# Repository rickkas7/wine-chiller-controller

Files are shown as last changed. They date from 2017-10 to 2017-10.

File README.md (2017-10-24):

# Wine chiller controller replacement

I have two Edgestar TWR282S thermoelectric wine chillers. One has wine in it, but the other I keep vegetables in, sort of like a root cellar.

They're over 10 years old, and I've been replacing parts on them for a while, but the case and doors are fine and the vegetable one has custom plexiglass shelves in it, so I hesitate to replace it.

I've replaced interior fans, [exterior fans](http://blog.rickk.com/food/2014/12/wine-chiller-exterior-fan-repair.html), and [Peltier chillers](http://blog.rickk.com/food/2013/06/repairing-a-wine-chiller.html), which are all pretty straightforward to do.

I also replaced the [controller boards](http://blog.rickk.com/food/2013/10/repairing-a-wine-chiller-part-2.html), which were available from Edgestar. They were kind of expensive at $48, and apparently not very durable, because one of the 4 year old replacements failed. And they're no longer available.

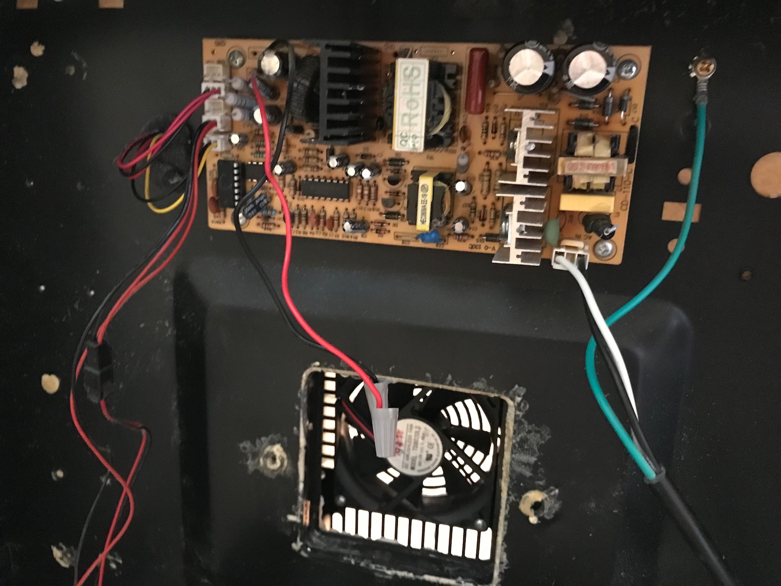
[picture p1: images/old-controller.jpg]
old controller


It appears the inductor failed. I might be able to just replace that but I have a better idea.

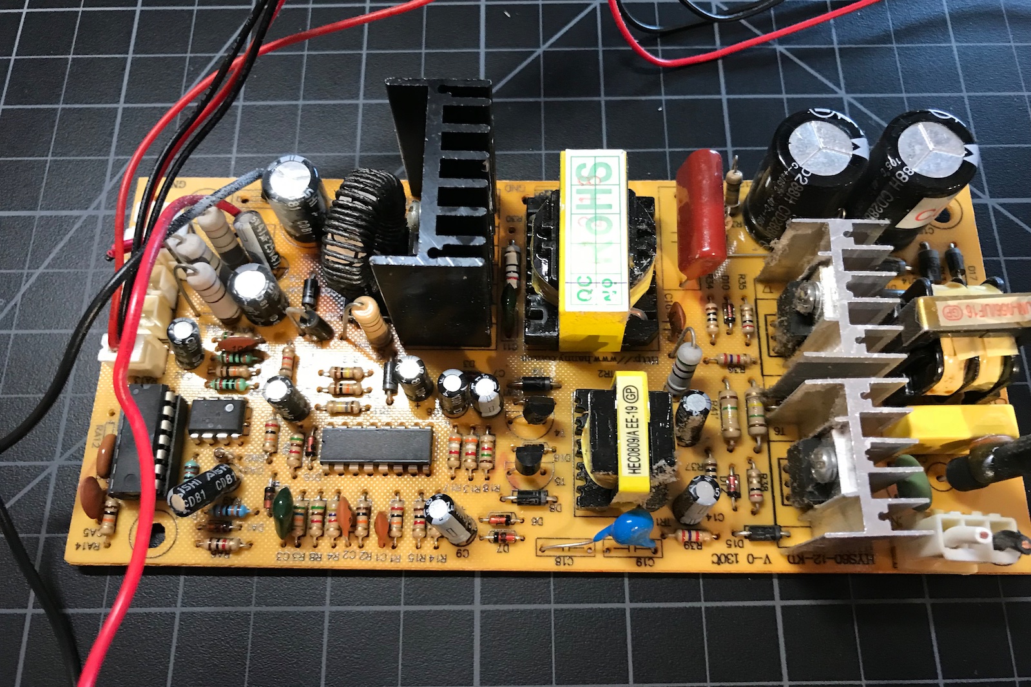
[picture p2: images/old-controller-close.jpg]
old controller close-up


I added a new power supply, controller board, and a fancy display that shows the temperature and also communicates the data so I can monitor the temperatures remotely!

The cyan LED to the right of the alphanumeric display turns red when the temperature is out of normal range.

I also get push notifications on my phone if the temperature goes way out of normal range.

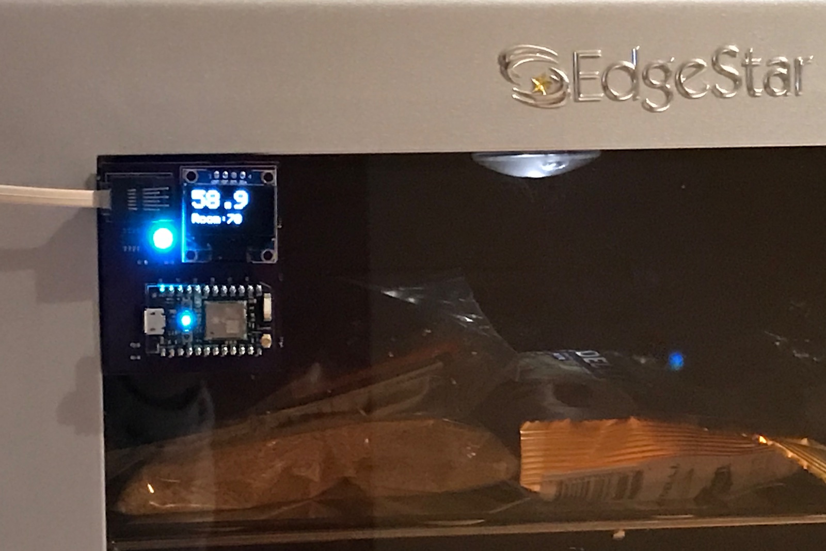
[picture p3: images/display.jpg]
display


## Power Supply

I replaced the power supply with a $14.98 12V 10A switching power supply that I got [from Amazon](https://www.amazon.com/LEDMO-Switching-Converter-Adapter-Transformer/dp/B01E6RMASC/ref=pd_ybh_a_4). It really only needs to be 5 to 6A, but the 10A was reasonably priced and offers a nice safety margin.

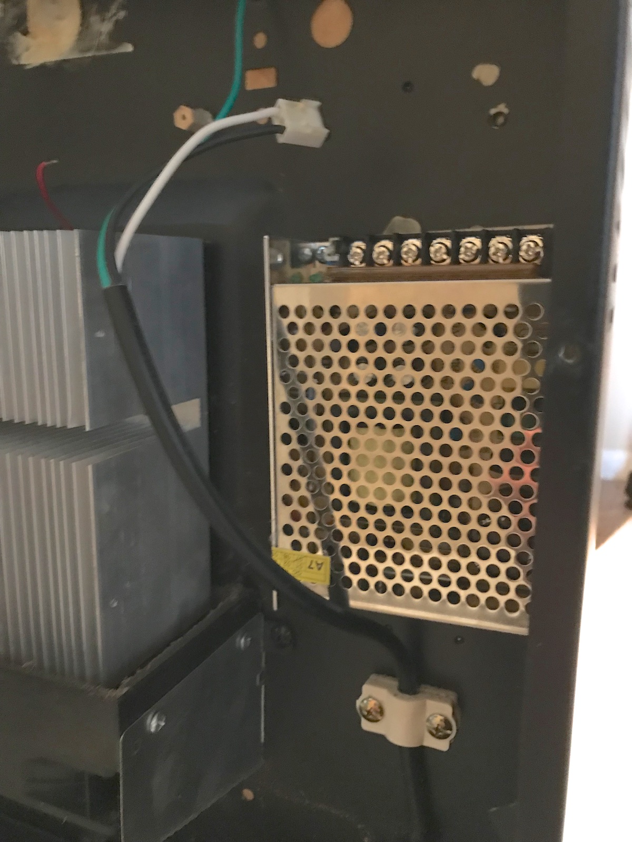
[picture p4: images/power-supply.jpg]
power supply


I was able to use the existing power cord, and I just replaced the connector with two spade lugs for connecting to the power supply. I also moved it from above the Peltier heat sink to the side, so hot air is not constantly blowing across it. The old location really seems suboptimal.

## Power Board

I made a power/controller board as well. It has a power supply for the display board, a bunch of handy connectors, a fuse, and a relay. 

In practice the Peltier is always on in my experience, but I did add a relay so it could be turned off in software, based on the thermometer reading inside the chiller. This allows for temperature control, and would also save some energy, as the Peltier by far uses the most energy, about 48 watts.
 
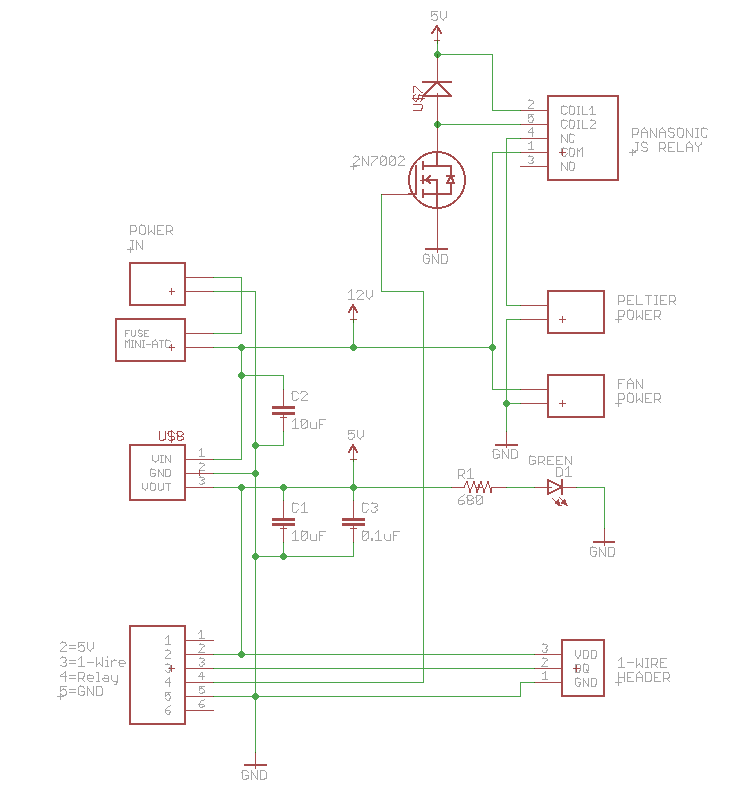
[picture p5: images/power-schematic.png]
power board schematic

 
This is the controller board with the 7 SMD components soldered to the board.

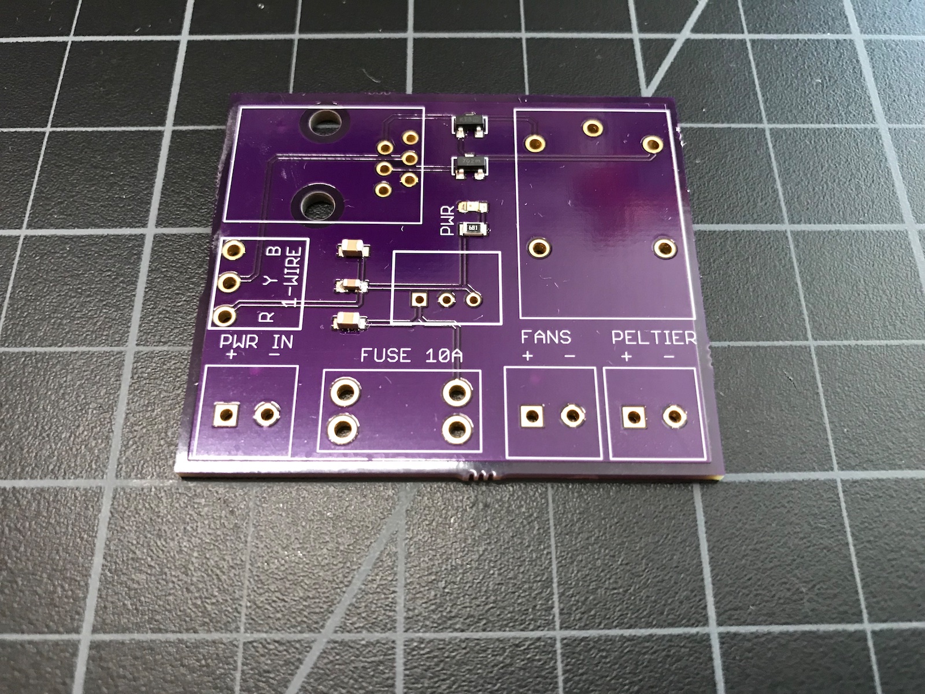
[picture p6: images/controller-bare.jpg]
controller bare board


And with all of the through-hole components soldered on.

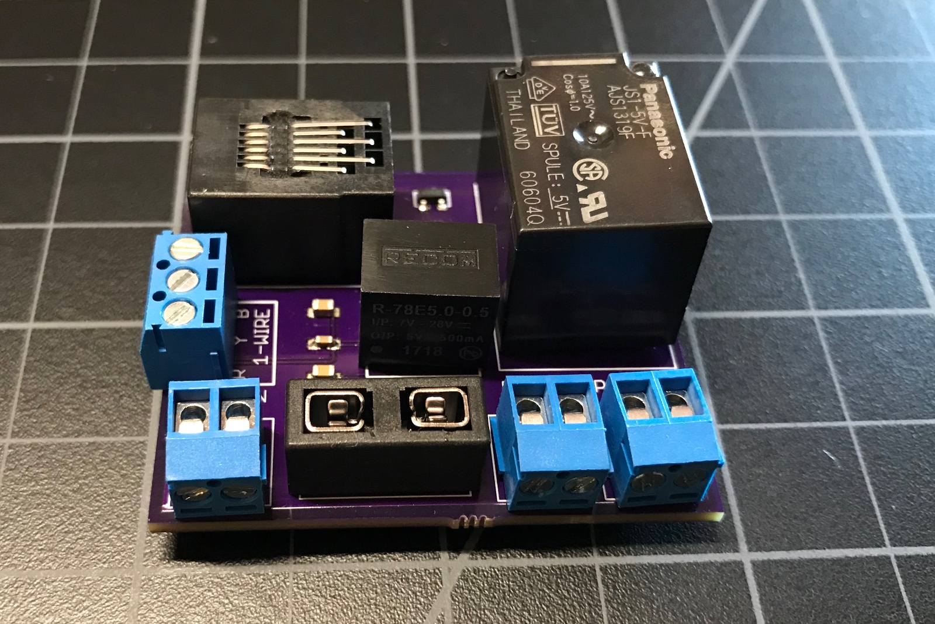
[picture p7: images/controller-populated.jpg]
controller populated board


Installed in the chiller.

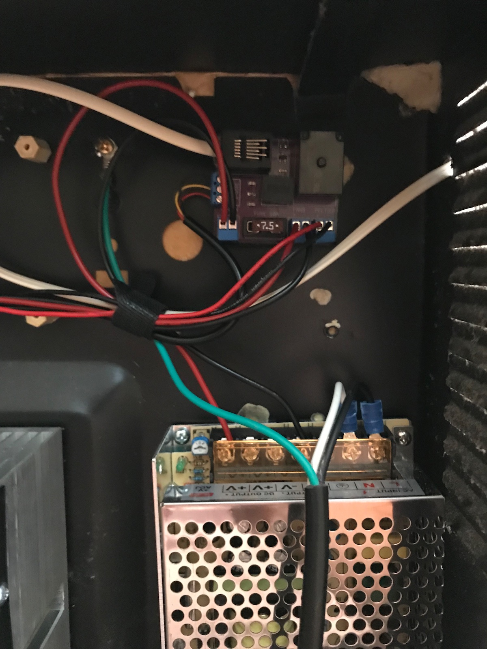
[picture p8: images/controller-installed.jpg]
controller installed


## Temperature sensor

I drilled a hole through the back of the chiller and used a weatherproof DS18B20 temperature sensor [from Amazon](https://www.amazon.com/Hilitchi-DS18B20-Waterproof-Temperature-Sensors/dp/B018KFX5X0/ref=sr_1_5). It was $12.99 for a set of 5 but I only needed 1 for this project.

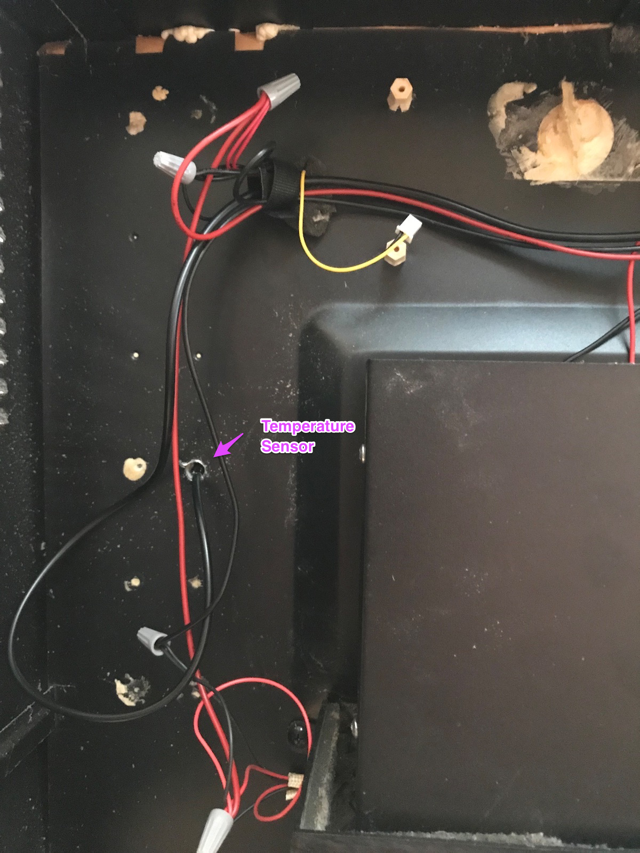
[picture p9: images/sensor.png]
temperature sensor


## Interior connections

Above the temperature sensor is the wiring that goes to the interior control box. There is one connector with 2 red wires and a black. And another connector with a black and yellow.

Connect all of the reds together; these are the +12V to the light and interior fan.

Connect all of the blacks together; these are the GND to the light and interior fan.

The yellow wire is for the temperature control inside; that's not used.

The light switch still works.

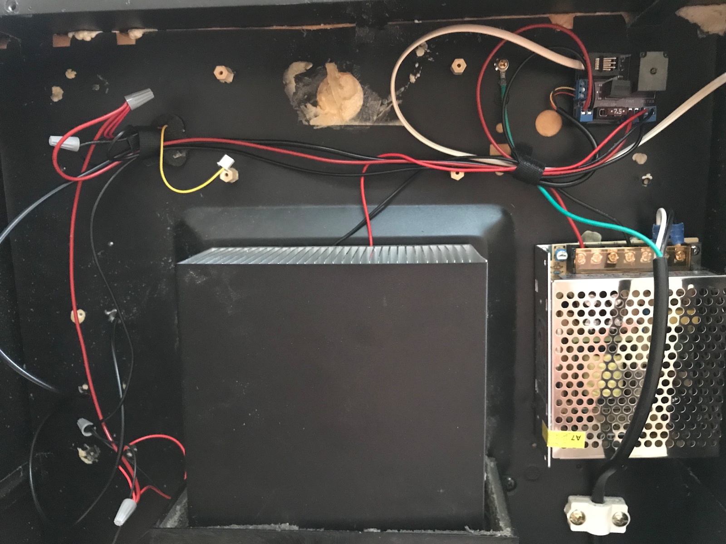
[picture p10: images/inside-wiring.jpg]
inside wiring


## Display board

The display board is mounted on the front of the chiller.

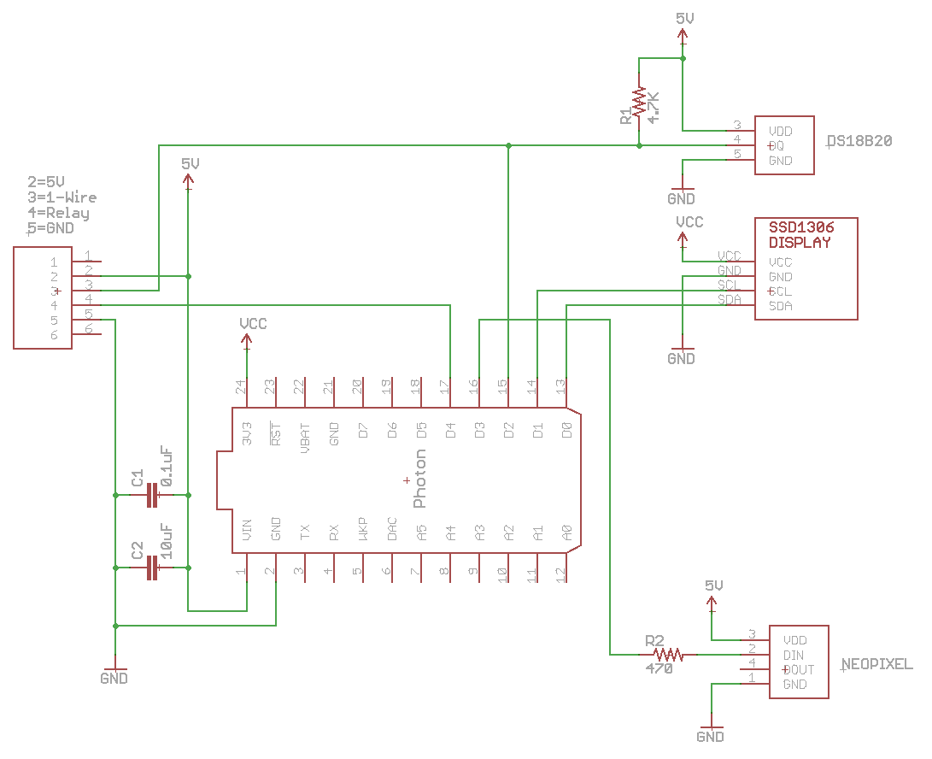
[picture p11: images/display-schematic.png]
display board schematic


Here's the display board with only the SMD components mounted. These include another DS18B20 temperature sensor (this time a 8-SOIC version) and a 4.7K pull-up resistor (0603 SMD) for the 1-Wire interface.

It also has a NeoPixel (WS2812) programmable LED and a 470 ohm series resistor for the data line (0603 SMD).

And power supply capacitors 0.1uF and 10 uF, and the SMD socket for the Particle Photon.

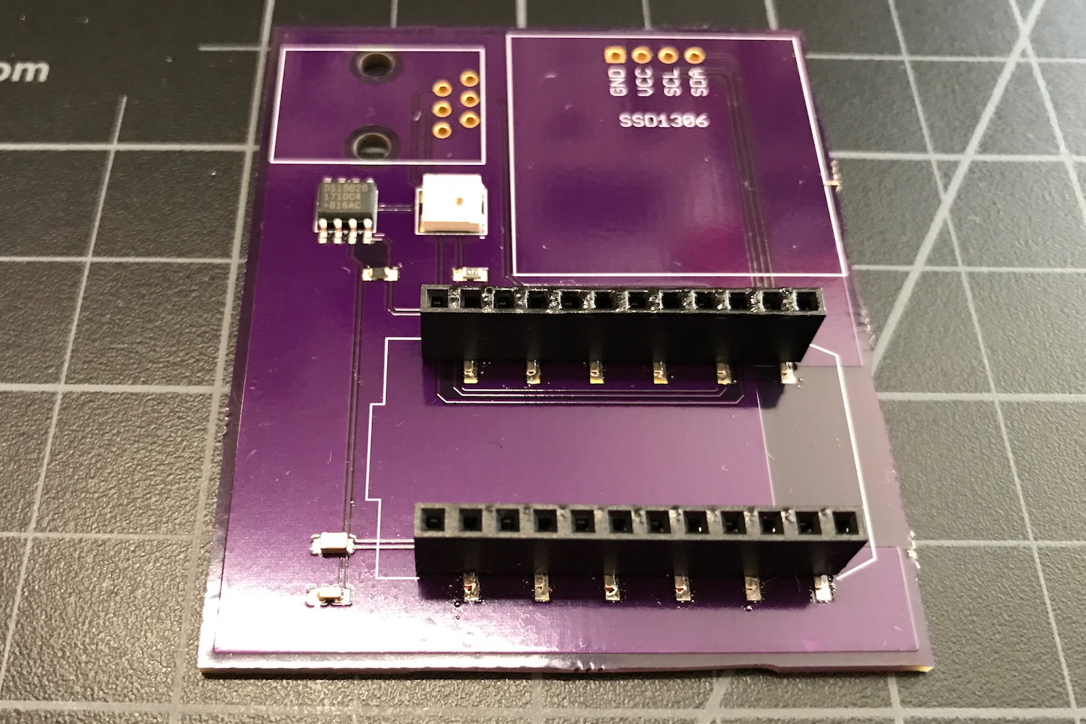
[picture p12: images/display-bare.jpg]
display board bare


There are also through-hole connectors for a modular jack and a SSD1306 display.

## Total Materials

This did cost more than the original controller, but it has a lot more features. In reality, you can just buy the power supply and wire it up with wire nuts and a little wire and it would cost maybe $16.

| Item | Source | Price |
|---|---|---|
| Power Supply | [Amazon](https://www.amazon.com/LEDMO-Switching-Converter-Adapter-Transformer/dp/B01E6RMASC/ref=pd_ybh_a_4) | 14.98 |
| Spade Lugs (2) | | $0.20<sup>1</sup> |
| ChillerPower Board | [OshPark](https://oshpark.com) | $4.90<sup>2</sup> |
| 2-conductor terminal blocks (3) | [DigiKey](https://www.digikey.com/product-detail/en/on-shore-technology-inc/OSTTF020161/ED2623-ND/614572) | $2.55 |
| 3-conductor terminal block | [DigiKey](https://www.digikey.com/product-detail/en/on-shore-technology-inc/OSTTE030161/ED2636-ND/614585) | $1.00 | 
| Modular Jack | [DigiKey](https://www.digikey.com/product-detail/en/stewart-connector/SS-7066-NF/380-1043-ND/388305) | $0.77 |
| Fuse holder | [DigiKey](https://www.digikey.com/product-detail/en/keystone-electronics/3568/36-3568-ND/2137306) | $0.98 |
| Fuse MiniATC 7.5A |  | $0.76<sup>1</sup> |
| Capacitor 10 uF 0805 | [DigiKey](https://www.digikey.com/product-detail/en/murata-electronics-north-america/GRM21BR61C106KE15L/490-3886-1-ND/965928) | $0.07<sup>4</sup> |
| Capacitor 0.1 uF | [DigiKey](https://www.digikey.com/product-detail/en/murata-electronics-north-america/GRM188R71C104KA01D/490-1532-1-ND/587771) | $0.03<sup>3</sup> |
| Resistor 680 ohm 0805 | [DigiKey](https://www.digikey.com/product-detail/en/panasonic-electronic-components/ERJ-6GEYJ681V/P680ACT-ND/90033) | $0.01<sup>3</sup> |
| Green LED 0603 | [DigiKey](https://www.digikey.com/product-detail/en/lite-on-inc/LTST-C193KGKT-5A/160-1828-1-ND/2356247) | $0.23<sup>5</sup> |
| Relay | [DigiKey](https://www.digikey.com/product-detail/en/panasonic-electric-works/JS1-5V-F/255-2064-ND/1242012) | $1.63 |
| Diode BAS21 | [DigiKey](http://www.digikey.com/product-detail/en/BAS21-7-F/BAS21-FDICT-ND/717813) | $0.14 |
| 2N7002 MOSFET | [DigiKey](https://www.digikey.com/product-detail/en/on-semiconductor/2N7002LT3G/2N7002LT3GOSCT-ND/2704932) | $0.16 |
| R-78-E Regulator | [DigiKey](https://www.digikey.com/product-detail/en/recom-power/R-78E5.0-0.5/945-1648-5-ND/2834904) | $2.84 |
| DS18B20 Weatherproof | [Amazon](https://www.amazon.com/Hilitchi-DS18B20-Waterproof-Temperature-Sensors/dp/B018KFX5X0/ref=sr_1_5) | $2.99<sup>6</sup> |
| ChillerDisplay Board | [OshPark](https://oshpark.com) | $8.31<sup>8</sup> |
| Photon Headers (2) | [DigiKey](https://www.digikey.com/product-detail/en/sullins-connector-solutions/NPTC121KFXC-RC/S5604-ND/776062) | $3.38 |
| Particle Photon | [Amazon](https://www.amazon.com/Particle-PHOTON-Comprehensive-Development-Access/dp/B016YNU1A0/ref=pd_ybh_a_5) | $19.00 | 
| NeoPixel | [DigiKey](https://www.digikey.com/product-detail/en/adafruit-industries-llc/1655/1528-1104-ND/5154679) | $0.45<sup>7</sup> |
| SSD1306 Display | [eBay](https://www.ebay.com/itm/391742247377) | $5.45 |
| Resistor 470 ohm | [DigiKey](https://www.digikey.com/product-detail/en/panasonic-electronic-components/ERJ-3GEYJ471V/P470GCT-ND/134802) | $0.01<sup>3</sup> |
| Resistor 4.7K ohm | [DigiKey](https://www.digikey.com/product-detail/en/panasonic-electronic-components/ERJ-PA3J472V/P4.7KBZCT-ND/5036332) | $0.01<sup>3</sup> |
| Capacitor 10 uF 0805 | [DigiKey](https://www.digikey.com/product-detail/en/murata-electronics-north-america/GRM21BR61C106KE15L/490-3886-1-ND/965928) | $0.07<sup>4</sup> |
| Capacitor 0.1 uF | [DigiKey](https://www.digikey.com/product-detail/en/murata-electronics-north-america/GRM188R71C104KA01D/490-1532-1-ND/587771) | $0.03<sup>3</sup> |
| Modular Jack | [DigiKey](https://www.digikey.com/product-detail/en/stewart-connector/SS-7066-NF/380-1043-ND/388305) | $0.77 |
| Wire Nuts (gray) |  | $0.50<sup>1</sup> |
| Hook-up Wire 18ga |  | $0.50<sup>1</sup> |
| Modular cable (4 conductor) |  | $2.00<sup>1</sup> |

Total: $72.72

<sup>1</sup>I had these on hand, I just guessed the price.

<sup>2</sup>The ChillerPower board has a minimum order of 3 at OshPark, so the actual cost was $14.70.

<sup>3</sup>I bought these in quantity 100 and divided the price. If you bought them in single quantities they'd be around $0.10 each.

<sup>4</sup>I bought these in quantity 100 and divided the price. If you bought them in single quantities they'd be around $0.21 each.

<sup>5</sup>I bought these in quantity 25 and divided the price. If you bought them in single quantities they'd be around $0.41 each.

<sup>6</sup>I bought these in quantity 5 and divided the price. Other vendors sell them in single quantities at a higher price.

<sup>7</sup>I bought these in quantity 10 and divided the price. That's the smallest package they're sold in.

<sup>8</sup>The ChillerDisplay board has a minimum order of 3 at OshPark, so the actual cost was $24.95.

## Firmware

I haven't included the firmware for the Photon. It's a simple matter of programming. No really, it uses standard libraries for the DS18B20 and SSD1306 and it should't be complicated.

The problem is that my code relies on a bunch of server infrastructure that's too complicated to share, and I didn't feel like writing a new set of firmware just for this post that I'd never use. I may change my mind later.

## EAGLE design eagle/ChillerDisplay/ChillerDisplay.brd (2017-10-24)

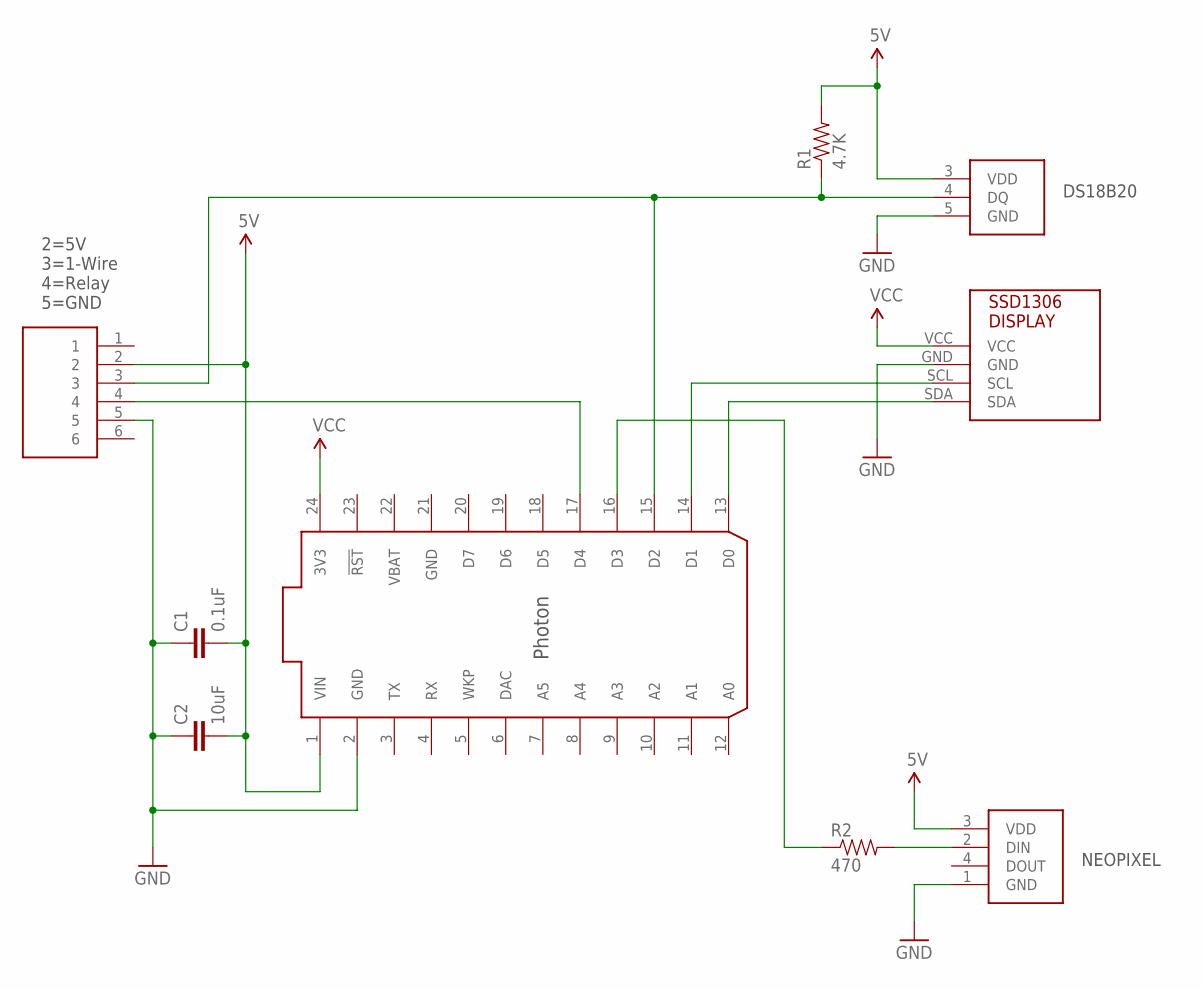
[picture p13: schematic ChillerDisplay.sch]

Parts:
C1: 0.1uF; 0603-CAP
C2: 10uF; 0603-CAP
J1: MODULAR-JACK-6P6C-1
R1: 4.7K; 0603-RES
R2: 470; 0603-RES
U$1: PHOTON; PHOTON-SMD
U$2: SSD1306REV-POL; SSD1306-REV-POL
U$3: DS18B208-SOIC; DS18B20-S0
U$4: SK6812

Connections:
5V: C1.2, C2.2, J1.2, R1.2, U$1.1 (VIN), U$3.3 (VDD), U$4.3 (VDD)
GND: C1.1, C2.1, J1.5, U$1.2 (GND), U$1.21 (GND), U$2.GND, U$3.5 (GND), U$4.1 (GND)
unnamed: U$1.13 (D0), U$2.SDA
unnamed: U$1.14 (D1), U$2.SCL
unnamed: J1.3, R1.1, U$1.15 (D2), U$3.4 (DQ)
unnamed: R2.2, U$4.2 (DIN)
unnamed: R2.1, U$1.16 (D3)
unnamed: J1.4, U$1.17 (D4)
VBAT: U$1.22 (VBAT)
VCC: U$1.24 (3V3), U$2.VCC

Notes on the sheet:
2=5V 3=1-Wire 4=Relay 5=GND
DS18B20
NEOPIXEL

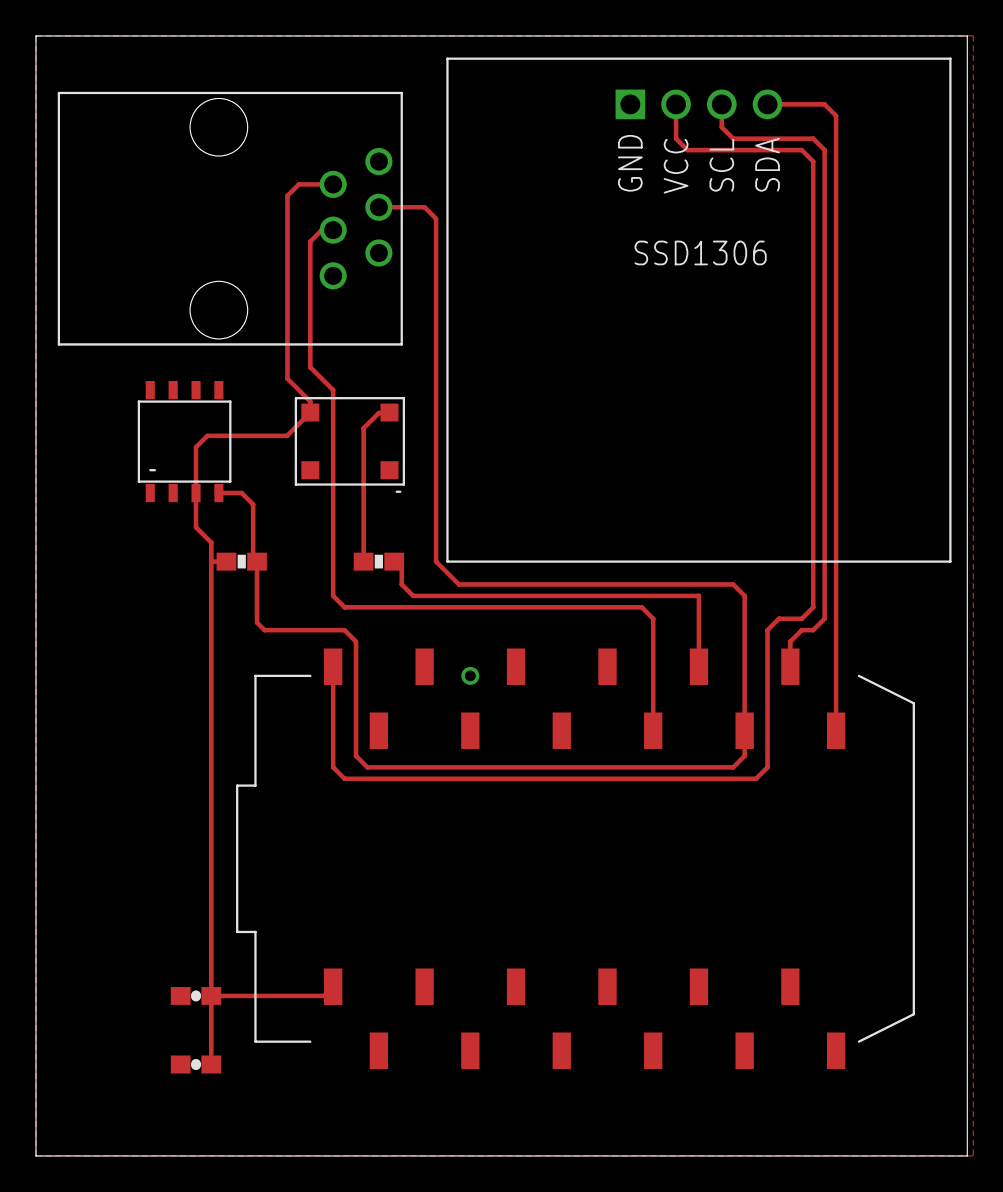
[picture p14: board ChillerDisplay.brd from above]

Board: 2 copper layers, 51.7 x 62.2 mm, 9 parts (0 on the bottom side), 9 nets.

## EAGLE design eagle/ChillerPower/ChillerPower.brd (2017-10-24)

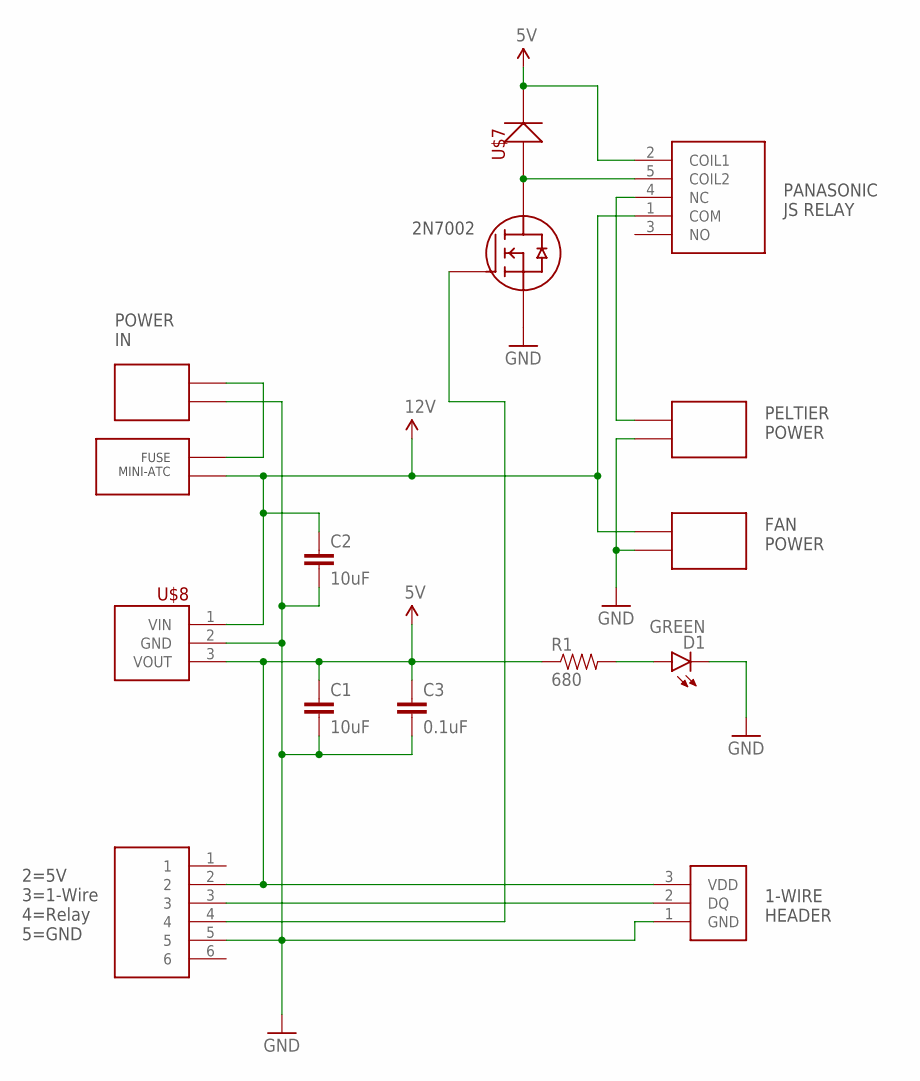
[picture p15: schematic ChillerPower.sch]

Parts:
C1, C2: 10uF; 0603-CAP
C3: 0.1uF; 0603-CAP
D1: GREEN; LED-0603
J1: MODULAR-JACK-6P6C-1
Q1: 2N7002L
R1: 680; 0805
U$1: FUSE-HOLDER-MINI-BLADE
U$2, U$4, U$5: TERMBLOCK-2X3.5MM
U$3: RELAY-PANASONIC-JS
U$6: TERMBLOCK-1WIRE
U$7: DIODE-BAS21
U$8: REG-R-78E

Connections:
5V: C1.1, C3.1, J1.2, R1.1, U$3.2 (COIL1), U$6.3 (VDD), U$7.3 (CA), U$8.3 (VOUT)
12V: C2.1, U$1.2, U$1.3 (2), U$3.1 (COM), U$5.1, U$8.1 (VIN)
GND: C1.2, C2.2, C3.2, D1.C, J1.5, Q1.2, U$2.2, U$4.2, U$5.2, U$6.1 (GND), U$8.2 (GND)
unnamed: U$1.1, U$1.4 (1), U$2.1
unnamed: Q1.3, U$3.5 (COIL2), U$7.1 (AN)
unnamed: J1.3, U$6.2 (DQ)
unnamed: U$3.4 (NC), U$4.1
unnamed: J1.4, Q1.1
unnamed: D1.A, R1.2

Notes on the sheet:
2=5V 3=1-Wire 4=Relay 5=GND
POWER IN
FAN POWER
PELTIER POWER
2N7002
1-WIRE HEADER
PANASONIC JS RELAY

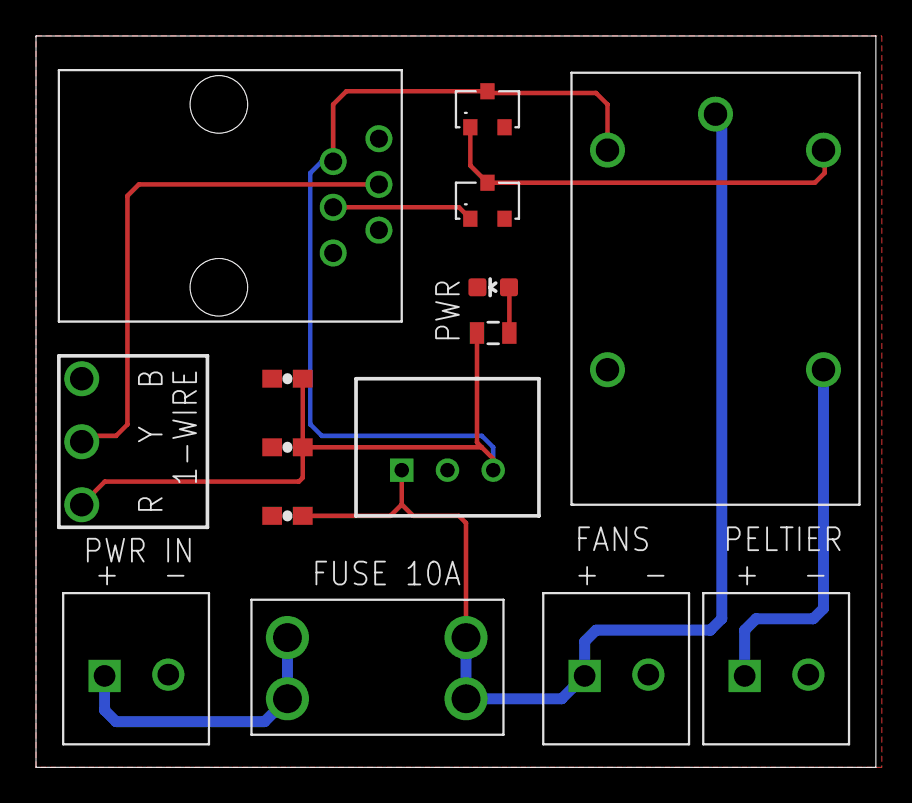
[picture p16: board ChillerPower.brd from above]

Board: 2 copper layers, 46.7 x 40.6 mm, 15 parts (0 on the bottom side), 9 nets.

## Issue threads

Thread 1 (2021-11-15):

How well is it working after 4 years?

guymcswain, 2021-11-15:
This is a very clever idea and I'm inspired to do something similar as my EdgeStar power supplies fail frequently and I'm tired of repairing them.  Thank you for sharing this.

My question is about reliability of the Thermo Electric Modules under digital on/off control.  The power supplies for these chillers are analog output - my unit seems to output between +12.5VDC (fully on) and hovers between 9-7V after achieving temperature.   I'd like to know if the TEMs can handle the 12V on 0V off modulation reliably.
